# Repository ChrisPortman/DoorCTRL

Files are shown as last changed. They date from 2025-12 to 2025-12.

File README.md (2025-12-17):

# DoorCTRL

## Overview

A simple device that functions as a controller for an electric door strike.

Rather than use a in-door mounted smart lock that requires batteries, I have an electric strike that
locks/unlocks (I have it setup to be locked by default) with the supply of 12v.  Additionally, I
have a magnetic reed switch that detects open/close state.

The device integrates with Home Assistant via MQTT.

## Motivation

Its very likely that something like Tasmota would have been able to be configured to do this job.
The main motivations were primarily around gaining experience in firmware development in Rust.

## Features

* Basic web interface supporting device control and configuration.
* Device initial setup mode. Device hosts a WiFi access point to connect to and perform initial
configuration.  The device's web interface in this mode can be reached on *http://192.168.0.1*.
Note the device does not provide DHCP, so the client will need to statically configure an IP address
on 192.168.0.0/24.
* Home Assistant integration via [MQTT with
discovery](https://www.home-assistant.io/integrations/mqtt/#mqtt-discovery) per .  MQTT supports TLS
(no certificate validation).
* *Factory* reset with long button push.
* Status indicator with RGB LED.

### LED Status

The following statuses are indicated by the RGB:

* Solid Red: Initialising
* Flashing Amber: unconfigured/setup mode
* Flashing Green: WiFi connected, MQTT not connected
* Solid Green: WiFi connected, MQTT connected.

## Hardware

This has been developed using a ESP32C3 development kit board that has a WS2812 RGB Led connected on
GPIO8.

Other GPIO assignments are:

* **GPIO1**: Triggers the lock.  Configured to pull Low so that the lock is triggered by setting the pin
  high.  Note that "triggered" depends on how the strike is set.  I.e. whether it is locks when
  powered or unlocked when powered.
* **GPIO2**: Monitors the reed switch interpreted as door open/closed.  Configured to pull high so
  the door registers as closed when grounded.
* **GPIO3**: Reset switch.  If held for 5 seconds, the current configuration is deleted and the
  device resets into setup mode.

The door lock in use is a [Lockwood ES110 Electric Strike](https://www.lockweb.com.au/au/en/products/electromechanical-solutions/electric-strikes/es110-series-electric-strike).  The reed is a cheap generic read from JayCar.

## Project Structure

The project is a workspace containing the following 2 crates:

1. `firmware`: this is mostly code that is specific to the ESP32C3 target and won't compile on
   *x86_64*.
2. `doorctrl`: this is code that will compile on *x86_64* and can therefore be easily tested.  The
   command alias `cargo test_pc` will run tests in this crate.

Generally the strategy has been to push as much code to `doorctrl` and call it from `firmware` to
facilitate testing.

An additional crate [weblite](https://docs.rs/weblite/latest/weblite/) was built as part of this,
but then pulled out and published independently as a simple `no_std` web framework, http protocol
and web socket protocol implementation.

## Screen Shots

Door open and locked:

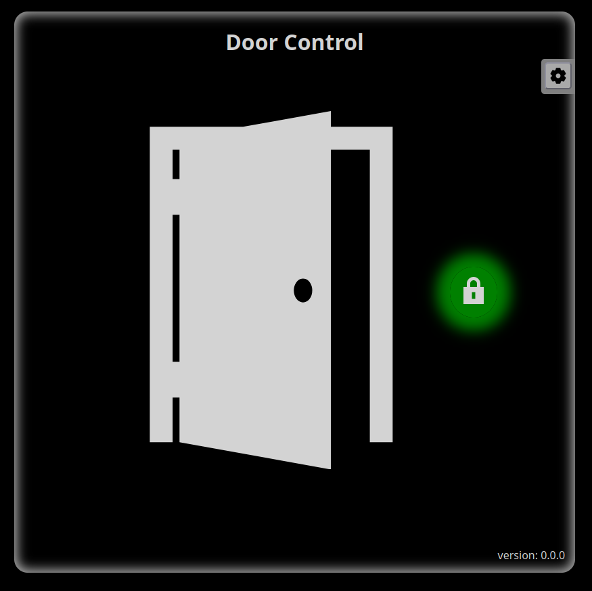
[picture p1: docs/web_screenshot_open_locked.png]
Open and Locked


Door closed and unlocked:

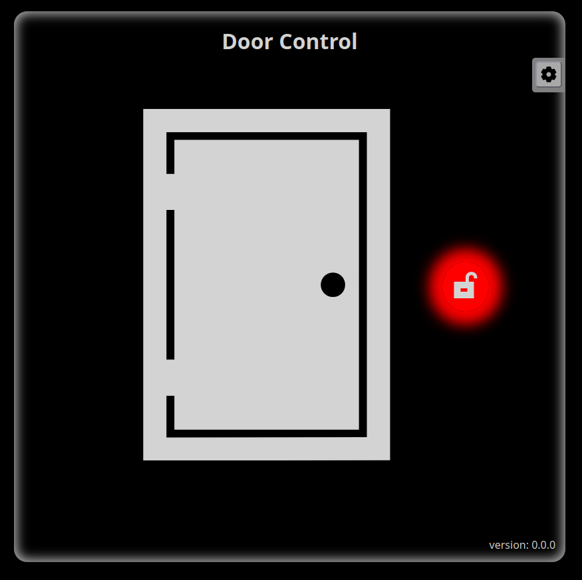
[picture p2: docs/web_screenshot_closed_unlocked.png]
Closed and Unlocked


Configuration settings:

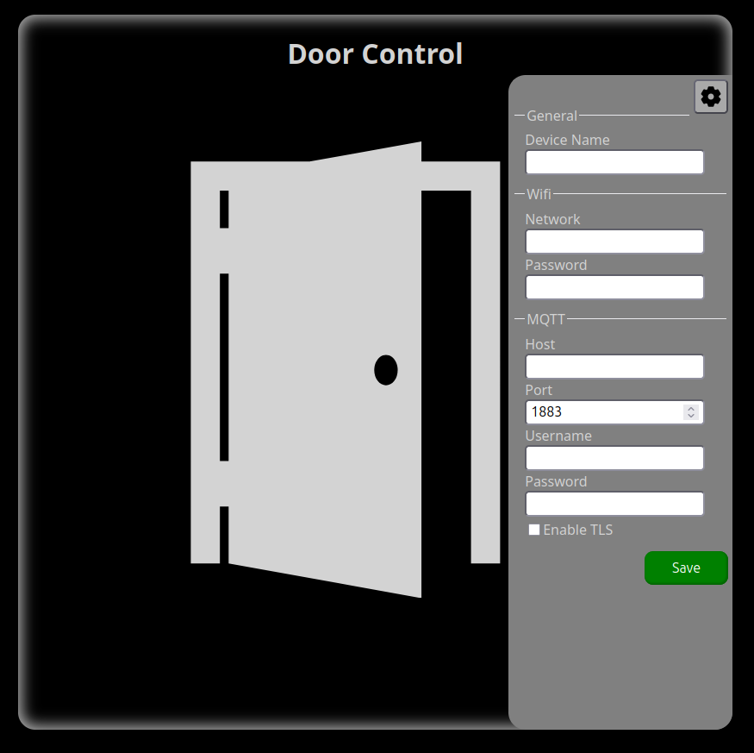
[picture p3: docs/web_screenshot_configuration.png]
Configuration Settings


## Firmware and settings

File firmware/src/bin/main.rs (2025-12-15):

#![no_std]
#![no_main]
#![deny(
    clippy::mem_forget,
    reason = "mem::forget is generally not safe to do with esp_hal types, especially those \
    holding buffers for the duration of a data transfer."
)]

use core::{
    net::{IpAddr, Ipv4Addr},
    ops::DerefMut,
    str::FromStr,
};
use defmt::{error, info, warn};
use embassy_executor::Spawner;
use embassy_futures::select;
use embassy_net::{
    tcp::{
        client::{TcpClient, TcpClientState, TcpConnection},
        TcpSocket,
    },
    IpListenEndpoint, Ipv4Cidr, Runner, Stack, StackResources, StaticConfigV4,
};
use embassy_sync::{
    blocking_mutex::raw::CriticalSectionRawMutex, channel::Channel, mutex::Mutex,
    pubsub::PubSubChannel,
};
use embassy_time::{Duration, Timer};

use embedded_nal_async::TcpConnect;
use embedded_storage::nor_flash::NorFlash;
use embedded_tls::{Aes128GcmSha256, NoVerify, TlsConfig, TlsConnection, TlsContext};

use esp_alloc as _;
use esp_bootloader_esp_idf::partitions::{self, FlashRegion, PartitionEntry};
use esp_hal::clock::{Clock, CpuClock};
use esp_hal::efuse::Efuse;
use esp_hal::gpio::{Input, InputConfig, Level, Output, OutputConfig, Pull};
#[cfg(target_arch = "riscv32")]
use esp_hal::interrupt::software::SoftwareInterruptControl;
use esp_hal::rng::{Rng, Trng};
use esp_hal::timer::timg::TimerGroup;

use esp_radio::{
    wifi::{
        AccessPointConfig, AuthMethod, ClientConfig, Interfaces, ModeConfig, ScanConfig,
        WifiApState, WifiController, WifiDevice, WifiEvent, WifiStaState,
    },
    Controller,
};
use esp_storage::FlashStorage;
use heapless::Vec;

use doorctrl::config::{ConfigV1, ConfigV1Value};
use doorctrl::door::Door;
use doorctrl::hass::MQTTContext;
use doorctrl::state::{AnyState, LockState};

use firmware::web::HttpClientHandler;
use firmware::ws2812::{Light, LightColor, LIGHT_UPDATE, WS2812B};
use firmware::{mk_static, ws2812::LightPattern};

const SOCKET_NUM: usize = 8;

// cmd_channel is for processing incomming command from external sources (i.e. lock/unlock)
static CMD_CHANNEL: Channel<CriticalSectionRawMutex, LockState, 2> =
    Channel::<CriticalSectionRawMutex, LockState, 2>::new();
// state_pubsub is for eminating changes in state as they are detected
static STATE_PUBSUB: PubSubChannel<CriticalSectionRawMutex, AnyState, 2, 6, 0> =
    PubSubChannel::<CriticalSectionRawMutex, AnyState, 2, 6, 0>::new();

#[panic_handler]
fn panic(_: &core::panic::PanicInfo) -> ! {
    loop {}
}

// This creates a default app-descriptor required by the esp-idf bootloader.
// For more information see: <https://docs.espressif.com/projects/esp-idf/en/stable/esp32/api-reference/system/app_image_format.html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>
esp_bootloader_esp_idf::esp_app_desc!();

fn u8_to_hex(u: u8) -> [u8; 2] {
    fn nybble_to_hex(n: u8) -> u8 {
        if n < 10 {
            // 40 is ascii 0
            return 48 + n;
        }

        // 97 is ascii 'a'
        97 + (n - 10)
    }

    let upper = u >> 4;
    let lower = u << 4 >> 4;

    [nybble_to_hex(upper), nybble_to_hex(lower)]
}

fn mac_to_hex(mac: [u8; 6]) -> [u8; 12] {
    let mut hex: [u8; 12] = [0; 12];
    for idx in 0..6 {
        let [upper, lower] = u8_to_hex(mac[idx]);
        hex[idx * 2] = upper;
        hex[idx * 2 + 1] = lower;
    }
    hex
}

type Storage = &'static Mutex<CriticalSectionRawMutex, FlashRegion<'static, FlashStorage<'static>>>;

fn prepare_flash(flash: &'static mut FlashStorage<'static>) -> Storage {
    let partition_buf = mk_static!(
        [u8; partitions::PARTITION_TABLE_MAX_LEN],
        [0u8; partitions::PARTITION_TABLE_MAX_LEN]
    );
    let partition_info = partitions::read_partition_table(flash, partition_buf).unwrap();
    let nvs = mk_static!(
        PartitionEntry<'static>,
        partition_info
            .find_partition(partitions::PartitionType::Data(
                partitions::DataPartitionSubType::Nvs,
            ))
            .unwrap()
            .unwrap()
    );
    let nvs_part = nvs.as_embedded_storage(flash);

    mk_static!(
        Mutex<CriticalSectionRawMutex, FlashRegion<'_, FlashStorage<'_>>>,
        Mutex::new(nvs_part)
    )
}

#[esp_rtos::main]
async fn main(spawner: Spawner) {
    // Real Time Trasfer protocol for probe-rs logging etc.
    rtt_target::rtt_init_defmt!();

    let hal_config = esp_hal::Config::default().with_cpu_clock(CpuClock::max());
    let peripherals = esp_hal::init(hal_config);
    esp_alloc::heap_allocator!(size: 72 * 1024);

    let timg0 = TimerGroup::new(peripherals.TIMG0);
    #[cfg(target_arch = "riscv32")]
    let sw_int = SoftwareInterruptControl::new(peripherals.SW_INTERRUPT);
    esp_rtos::start(
        timg0.timer0,
        #[cfg(target_arch = "riscv32")]
        sw_int.software_interrupt0,
    );

    // Init RGB
    let light = Light {
        inner: WS2812B::new(
            peripherals.RMT,
            CpuClock::_80MHz.frequency().as_mhz(),
            peripherals.GPIO8,
        )
        .expect("create LED failed"),
    };
    spawner.spawn(blink(light)).expect("failed to spawn blink");
    LIGHT_UPDATE.signal(LightPattern::Solid(LightColor::red()));

    // Flash Memory
    let flash = mk_static!(FlashStorage, FlashStorage::new(peripherals.FLASH));
    let storage = prepare_flash(flash);

    let rst_pin = Input::new(
        peripherals.GPIO3,
        InputConfig::default().with_pull(Pull::Up),
    );

    // Init the door
    let lock_pin = Output::new(peripherals.GPIO1, Level::Low, OutputConfig::default());
    let reed_pin = Input::new(
        peripherals.GPIO2,
        InputConfig::default().with_pull(Pull::Up),
    );
    let door = Door::new(
        lock_pin,
        reed_pin,
        CMD_CHANNEL.receiver(),
        STATE_PUBSUB.immediate_publisher(),
    );
    spawner.spawn(door_service(door)).ok();

    // Init wifi hardware
    let esp_radio_ctrl = &*mk_static!(Controller<'static>, esp_radio::init().unwrap());
    let (controller, interfaces) =
        esp_radio::wifi::new(esp_radio_ctrl, peripherals.WIFI, Default::default()).unwrap();

    let mut locked_storage = storage.lock().await;
    let config = ConfigV1::load(locked_storage.deref_mut());
    drop(locked_storage);

    match config {
        Ok(cfg) => {
            info!("config ready, entering normal mode");
            normal_mode(spawner, cfg, controller, interfaces, storage, rst_pin).await
        }
        Err(e) => {
            warn!("config not ready ({}), entering setup mode", e);
            setup_mode(spawner, controller, interfaces, storage).await;
        }
    };

    loop {
        Timer::after(Duration::from_secs(1)).await;
    }
}

async fn normal_mode(
    spawner: Spawner,
    config: ConfigV1,
    controller: WifiController<'static>,
    interfaces: Interfaces<'static>,
    storage: Storage,
    rst_pin: Input<'static>,
) {
    if let Err(e) = spawner.spawn(factory_resetter(rst_pin, storage)) {
        error!("error spawning reset monitor: {}", e);
    }

    let rng = Rng::new();
    let seed = (rng.random() as u64) << 32 | rng.random() as u64;
    let device_id = mk_static!([u8; 12], mac_to_hex(Efuse::read_base_mac_address()));
    let wifi_interface = interfaces.sta;
    let net_config = embassy_net::Config::dhcpv4(Default::default());

    spawner
        .spawn(wifi_client(controller, config.wifi_ssid, config.wifi_pass))
        .ok();

    let (stack, runner) = embassy_net::new(
        wifi_interface,
        net_config,
        mk_static!(
            StackResources<SOCKET_NUM>,
            StackResources::<SOCKET_NUM>::new()
        ),
        seed,
    );
    spawner.spawn(net_task(runner)).ok();

    stack.wait_link_up().await;
    info!("Wifi connected");
    LIGHT_UPDATE.signal(LightPattern::Blink(
        LightColor::green(),
        Duration::from_millis(500),
        Duration::from_millis(500),
    ));

    stack.wait_config_up().await;
    info!("IP config applied {}", stack.config_v4().unwrap().address);

    if let Err(e) = spawner.spawn(mqtt_service(device_id, config, stack)) {
        error!("error spanning MQTT client: {}", e);
    }

    let cmd_sender = CMD_CHANNEL.sender();

    let http_server = mk_static!(
        weblite::server::Server::<HttpClientHandler>,
        weblite::server::Server::<_>::new(HttpClientHandler::new(
            firmware::web::HttpServiceState {
                storage,
                config,
                door_state: None,
                lock_state: None,
            },
            cmd_sender,
            &STATE_PUBSUB,
        ))
    );

    for _ in 0..4 {
        info!("starting a web server task");
        if let Err(e) = spawner.spawn(http_connection(stack, http_server)) {
            error!("error spawning web task: {}", e);
        }
    }
}

async fn setup_mode(
    spawner: Spawner,
    controller: WifiController<'static>,
    interfaces: Interfaces<'static>,
    storage: Storage,
) {
    let rng = Rng::new();
    let seed = (rng.random() as u64) << 32 | rng.random() as u64;
    let wifi_interface = interfaces.ap;
    let net_config = embassy_net::Config::ipv4_static(StaticConfigV4 {
        address: Ipv4Cidr::new(Ipv4Addr::new(192, 168, 0, 1), 24),
        gateway: None,
        dns_servers: Vec::<_, 3>::new(),
    });
    let config = ConfigV1::default();

    spawner.spawn(wifi_ap(controller)).ok();

    let (stack, runner) = embassy_net::new(
        wifi_interface,
        net_config,
        mk_static!(
            StackResources<SOCKET_NUM>,
            StackResources::<SOCKET_NUM>::new()
        ),
        seed,
    );

    spawner.spawn(net_task(runner)).ok();

    let cmd_sender = CMD_CHANNEL.sender();

    let http_server = mk_static!(
        weblite::server::Server::<HttpClientHandler>,
        weblite::server::Server::<_>::new(HttpClientHandler::new(
            firmware::web::HttpServiceState {
                storage,
                config,
                door_state: None,
                lock_state: None,
            },
            cmd_sender,
            &STATE_PUBSUB,
        ))
    );

    for _ in 0..4 {
        info!("starting a web server task");
        if let Err(e) = spawner.spawn(http_connection(stack, http_server)) {
            error!("error spawning web task: {}", e);
        }
    }
}

#[embassy_executor::task]
async fn wifi_ap(mut controller: WifiController<'static>) -> ! {
    info!("Device capabilities: {:?}", controller.capabilities());
    loop {
        if esp_radio::wifi::ap_state() == WifiApState::Started {
            // wait until we're no longer connected
            controller.wait_for_event(WifiEvent::ApStop).await;
            Timer::after(Duration::from_millis(5000)).await
        }

        if !matches!(controller.is_started(), Ok(true)) {
            let ap_config = AccessPointConfig::default()
                .with_ssid("DoorControl".into())
                .with_auth_method(AuthMethod::Wpa2Personal)
                .with_password("new_door_control".into());
            let client_config = ModeConfig::AccessPoint(ap_config);

            if let Err(e) = controller.set_config(&client_config) {
                error!("wifi AP configuration error: {}", e);
            }
            controller.start_async().await.unwrap();
            info!("Wifi AP started!");
            LIGHT_UPDATE.signal(LightPattern::Blink(
                LightColor::amber(),
                Duration::from_millis(500),
                Duration::from_millis(500),
            ));
        }
    }
}

#[embassy_executor::task]
async fn wifi_client(
    mut controller: WifiController<'static>,
    ssid: ConfigV1Value,
    pass: ConfigV1Value,
) -> ! {
    loop {
        if esp_radio::wifi::sta_state() == WifiStaState::Connected {
            // wait until we're no longer connected
            controller.wait_for_event(WifiEvent::StaDisconnected).await;
            Timer::after(Duration::from_millis(5000)).await
        }

        if !matches!(controller.is_started(), Ok(true)) {
            let client_config = ModeConfig::Client(
                ClientConfig::default()
                    .with_ssid(ssid.as_str().into())
                    .with_password(pass.as_str().into()),
            );

            if let Err(e) = controller.set_config(&client_config) {
                error!("wifi station configuration error: {}", e);
            }

            controller.start_async().await.unwrap();

            let scan_config = ScanConfig::default().with_max(10);
            let result = controller
                .scan_with_config_async(scan_config)
                .await
                .unwrap();
            for ap in result {
                info!("Found SSID: {}", ap.ssid);
            }
        }
        info!("WIFI connecting ...");

        match controller.connect_async().await {
            Ok(_) => {
                info!("Wifi connected!");
                LIGHT_UPDATE.signal(LightPattern::Solid(LightColor::amber()));
            }
            Err(e) => {
                info!("Failed to connect to wifi: {:?}", e);
                Timer::after(Duration::from_millis(5000)).await
            }
        }
    }
}

#[embassy_executor::task]
async fn mqtt_service(device_id: &'static [u8; 12], config: ConfigV1, stack: Stack<'static>) -> ! {
    let mut context = MQTTContext::new(
        device_id,
        config.device_name.as_str(),
        config.mqtt_user.as_str(),
        config.mqtt_pass.as_str(),
    );

    let mqtt_ipaddr = match Ipv4Addr::from_str(config.mqtt_host.as_str()) {
        Ok(i) => i,
        Err(_) => {
            loop {
                // Never progress...
                error!("mqtt host is not a valid IP address");
                Timer::after(Duration::from_secs(3600)).await;
            }
        }
    };

    let mut tls_read_buf = [0u8; 16640];
    let mut tls_write_buf = [0u8; 16640];

    let state = TcpClientState::<3, 1024, 1024>::new();
    loop {
        stack.wait_link_up().await;
        stack.wait_config_up().await;

        let sock = TcpClient::new(stack, &state);
        info!("MQTT: connecting to {}", mqtt_ipaddr);
        let conn = match sock
            .connect(core::net::SocketAddr::new(
                IpAddr::V4(mqtt_ipaddr),
                config.mqtt_port,
            ))
            .await
        {
            Ok(c) => c,
            Err(e) => {
                info!("failed to connect MQTT: {}", e);
                Timer::after(Duration::from_secs(5)).await;
                continue;
            }
        };

        match config.mqtt_tls {
            true => {
                let mut rng = Trng::try_new().unwrap();
                let tls_config = TlsConfig::new().with_server_name(config.mqtt_host.as_str());
                let mut tls_conn =
                    TlsConnection::<TcpConnection<'_, 3, 1024, 1024>, Aes128GcmSha256>::new(
                        conn,
                        tls_read_buf.as_mut_slice(),
                        tls_write_buf.as_mut_slice(),
                    );

                match tls_conn
                    .open::<Trng, NoVerify>(TlsContext::new(&tls_config, &mut rng))
                    .await
                {
                    Err(e) => error!("could not establish TLS connection to MQTT broker: {}", e),
                    Ok(()) => {
                        info!("TLS connection to MQTT");

                        LIGHT_UPDATE.signal(LightPattern::Solid(LightColor::green()));
                        if let Err(e) = context
                            .run(
                                tls_conn,
                                &CMD_CHANNEL.sender(),
                                &mut STATE_PUBSUB.subscriber().unwrap(),
                            )
                            .await
                        {
                            error!("MQTT session error: {}", e);
                        }
                    }
                }
            }
            false => {
                info!("TCP connection to MQTT");
                LIGHT_UPDATE.signal(LightPattern::Solid(LightColor::green()));
                if let Err(e) = context
                    .run(
                        conn,
                        &CMD_CHANNEL.sender(),
                        &mut STATE_PUBSUB.subscriber().unwrap(),
                    )
                    .await
                {
                    error!("MQTT session error: {}", e);
                }
            }
        }

        Timer::after(Duration::from_secs(5)).await;
    }
}

#[embassy_executor::task(pool_size = 4)]
async fn http_connection(
    stack: Stack<'static>,
    http_server: &'static weblite::server::Server<HttpClientHandler>,
) -> ! {
    let mut tx_buf = [0u8; 1024];
    let mut rx_buf = [0u8; 1024];
    let mut http_buff = [0u8; 1024];

    loop {
        stack.wait_link_up().await;
        stack.wait_config_up().await;

        let mut conn = TcpSocket::new(stack, rx_buf.as_mut_slice(), tx_buf.as_mut_slice());
        if let Err(e) = conn
            .accept(IpListenEndpoint {
                addr: None,
                port: 80,
            })
            .await
        {
            error!("error accepting http connection: {}", e);
            Timer::after(Duration::from_secs(5)).await;
            continue;
        }

        if let Err(e) = http_server.serve(&mut conn, http_buff.as_mut_slice()).await {
            error!("HTTP error: {}", e);
        }

        Timer::after(Duration::from_secs(5)).await;
    }
}

#[embassy_executor::task]
async fn door_service(
    mut door: Door<'static, Output<'static>, Input<'static>, CriticalSectionRawMutex>,
) -> ! {
    loop {
        door.run().await;
    }
}

#[embassy_executor::task]
async fn net_task(mut runner: Runner<'static, WifiDevice<'static>>) -> ! {
    runner.run().await
}

#[embassy_executor::task]
async fn factory_resetter(mut pin: Input<'static>, storage: Storage) -> ! {
    loop {
        pin.wait_for_low().await;
        info!("reset button pushed");
        let action =
            select::select(pin.wait_for_high(), Timer::after(Duration::from_secs(5))).await;

        match action {
            select::Either::First(_) => {
                // Pin went high (button released) before 5 secs
                info!("reset button released before timeout, not resetting");
            }
            select::Either::Second(_) => {
                // Held low for long enough. Delete config and reset.
                info!("reset button held for 5 seconds, resetting");

                {
                    let mut locked_storage = storage.lock().await;
                    if let Err(e) = locked_storage.erase(0, 4096) {
                        error!("failed to erase storage before reset: {}", e);
                    }
                }

                esp_hal::system::software_reset();
            }
        }
    }
}

#[embassy_executor::task]
async fn blink(mut led: Light<'static>) -> ! {
    info!("initializing LED");
    led.run(LightPattern::Off).await;
}

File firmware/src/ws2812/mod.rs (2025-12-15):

use defmt::error;
use embassy_futures::select::{self, select};
use embassy_sync::blocking_mutex::raw::CriticalSectionRawMutex;
use embassy_sync::signal::Signal;
use embassy_time::{Duration, Timer};
use esp_hal::gpio::{Level, Output, OutputConfig, OutputPin};
use esp_hal::peripherals::RMT;
use esp_hal::rmt::{Channel, PulseCode, Rmt, Tx, TxChannelConfig, TxChannelCreator};
use esp_hal::time::Rate;
use esp_hal::Async;

const BRG_MAX_NUM_OF_LEDS: usize = 256;
const BRG_PACKET_SIZE: usize = 24;

#[derive(Debug, defmt::Format)]
pub enum Error {
    TooManyLeds,
    RmtError(esp_hal::rmt::Error),
}

// 'From' trait
impl From<esp_hal::rmt::Error> for Error {
    fn from(err: esp_hal::rmt::Error) -> Self {
        Error::RmtError(err)
    }
}

pub struct WS2812B<'a> {
    red: u8,
    green: u8,
    blue: u8,
    ch: Channel<'a, Async, Tx>,
}

impl<'a> WS2812B<'a> {
    /// Create a WS2812B instance with RGB(0, 0, 0)
    ///
    /// Here's an example:
    ///
    /// ```
    /// let mut led = WS2812B::new(peripherals.RMT, 80, peripherals.GPIO8)?;
    /// ```
    pub fn new<P>(rmt: RMT<'a>, freq_mhz: u32, gpio: P) -> Result<Self, Error>
    where
        P: OutputPin + 'a,
    {
        let rmt = Rmt::new(rmt, Rate::from_mhz(freq_mhz))?.into_async();
        let output: Output<'_> = Output::new(gpio, Level::High, OutputConfig::default());
        let tick_rate: u32 = (freq_mhz * 5) / 100; // 50 ns tick!
        let channel = rmt.channel0.configure_tx(
            output,
            TxChannelConfig::default().with_clk_divider(tick_rate as u8),
        )?;

        Ok(WS2812B {
            red: u8::default(),
            green: u8::default(),
            blue: u8::default(),
            ch: channel,
        })
    }

    pub async fn set_colors(&mut self, r: u8, g: u8, b: u8) -> Result<(), Error> {
        self.red = r;
        self.green = g;
        self.blue = b;

        self.play(1).await
    }

    pub async fn set_red(&mut self, r: u8) -> Result<(), Error> {
        self.set_colors(r, 0, 0).await
    }

    pub async fn set_green(&mut self, g: u8) -> Result<(), Error> {
        self.set_colors(0, g, 0).await
    }

    pub async fn set_blue(&mut self, b: u8) -> Result<(), Error> {
        self.set_colors(0, 0, b).await
    }

    pub async fn play(&mut self, num: usize) -> Result<(), Error> {
        if num >= BRG_MAX_NUM_OF_LEDS - 1 {
            return Err(Error::TooManyLeds);
        }

        // Create final stream of data.
        let mut data: [PulseCode; BRG_PACKET_SIZE * BRG_MAX_NUM_OF_LEDS] =
            [PulseCode::default(); BRG_PACKET_SIZE * BRG_MAX_NUM_OF_LEDS];

        // Create RGB packet. (Always the same for now.)
        let packet = self.build_packet();

        for i in 0..num {
            let index = i * BRG_PACKET_SIZE;
            data[index..(index + BRG_PACKET_SIZE)].copy_from_slice(&packet);
        }

        data[num * BRG_PACKET_SIZE] = PulseCode::end_marker();
        // Slice one index extra to fit the `PulseCode::empty()`;
        self.dispatch(&data[0..((num * BRG_PACKET_SIZE) + 1)])
            .await?;

        Ok(())
    }

    async fn dispatch(&mut self, data: &[PulseCode]) -> Result<(), Error> {
        self.ch.transmit(data).await?;
        Ok(())
    }

    // Reference https://cdn-shop.adafruit.com/datasheets/WS2812.pdf
    // in ns: 700/600
    fn get_bit_one(&self) -> PulseCode {
        PulseCode::new(Level::High, 14, Level::Low, 12)
    }

    // in ns: 350/800
    fn get_bit_zero(&self) -> PulseCode {
        // PulseCode::new(Level::High, 8, Level::Low, 17)
        PulseCode::new(Level::High, 7, Level::Low, 16)
    }

    fn build_packet(&self) -> [PulseCode; BRG_PACKET_SIZE] {
        let mut data: [PulseCode; BRG_PACKET_SIZE] = [PulseCode::default(); BRG_PACKET_SIZE];
        let mut index: usize = 0;

        for byte in &[self.green, self.red, self.blue] {
            for bit_index in (0..8).rev() {
                if (*byte >> bit_index) & 0x01 == 0x01 {
                    data[index] = self.get_bit_one();
                } else {
                    data[index] = self.get_bit_zero();
                }
                index += 1;
            }
        }

        data
    }
}

const LIGHT_INTENSITY_DEFAULT: u8 = 32;

pub static LIGHT_UPDATE: Signal<CriticalSectionRawMutex, LightPattern> = Signal::new();

#[derive(Default)]
pub struct LightColor {
    pub r: u8,
    pub g: u8,
    pub b: u8,
}

impl LightColor {
    pub fn off() -> Self {
        Self::default()
    }

    pub fn red() -> Self {
        Self::default().with_red(LIGHT_INTENSITY_DEFAULT)
    }

    pub fn green() -> Self {
        Self::default().with_green(LIGHT_INTENSITY_DEFAULT)
    }

    pub fn blue() -> Self {
        Self::default().with_blue(LIGHT_INTENSITY_DEFAULT)
    }

    pub fn amber() -> Self {
        Self::default()
            .with_red(LIGHT_INTENSITY_DEFAULT)
            .with_green(16)
    }

    fn with_red(mut self, r: u8) -> Self {
        self.r = r;
        self
    }
    fn with_green(mut self, g: u8) -> Self {
        self.g = g;
        self
    }
    fn with_blue(mut self, b: u8) -> Self {
        self.b = b;
        self
    }
}

pub enum LightPattern {
    Off,
    Solid(LightColor),
    // Blink(color, on_time, off_time)
    Blink(LightColor, Duration, Duration),
    BlinkCode(LightColor, u8),
}

pub struct Light<'a> {
    pub inner: WS2812B<'a>,
}
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
